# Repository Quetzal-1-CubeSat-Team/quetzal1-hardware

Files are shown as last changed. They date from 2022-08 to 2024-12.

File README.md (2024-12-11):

# Quetzal-1 Hardware

<p align="center">
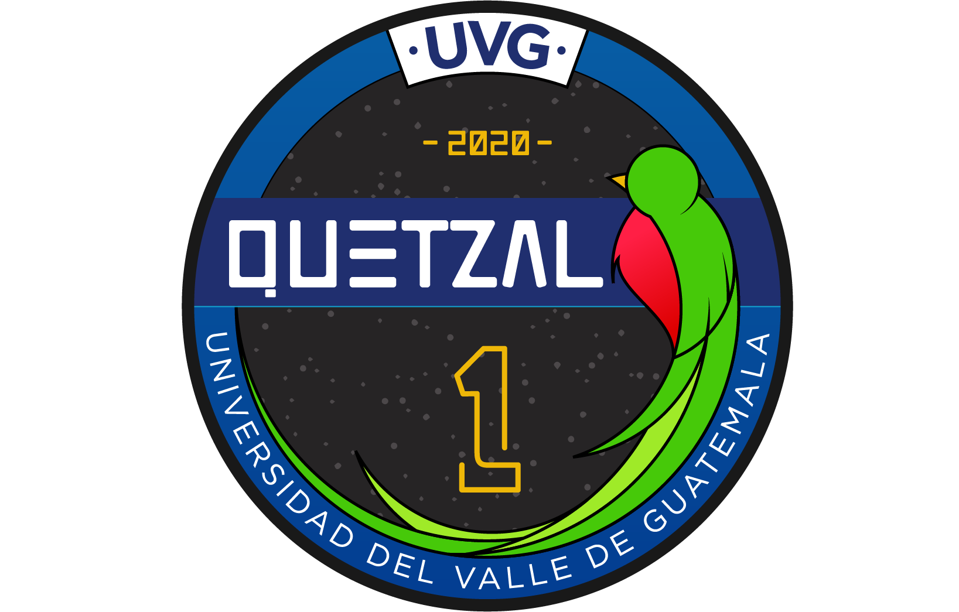
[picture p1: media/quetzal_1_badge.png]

</p>

### 📫 Contact Us!

If the information published here was helpful, we'd love to know! Contact us below and let us know how we can help 🙋‍♀️🙋‍♂️!

1. 💌 **Email us:** [satelite@uvg.edu.gt](mailto:satelite@uvg.edu.gt)
2. 🐦 **Reach out on X:** [@quetzal1_uvg](https://x.com/quetzal1_uvg)

For an overview of Quetzal-1, [read our profile!](https://github.com/Quetzal-1-CubeSat-Team)

## Directory Description

This repository serves as the central location for all hardware design files for the Quetzal-1 satellite. We are indebted to the open-source community, as a large part of the hardware and software was inspired and based on open-source platforms, such as [Arduino](https://www.arduino.cc/), and libraries written by its ever-expanding community.

The hardware files for the following subsystems are included in this repository:

1. [ADCS](./ADCS/): contains the hardware design files for the Attitude Determination and Control System (ADCS).
2. [EPS](./EPS/): contains the hardware design files for the Electrical Power System (EPS).
3. [ADM](./ADM/): contains the hardware design files for the Antenna Deployment Mechanism (ADM).
4. [media](./media/): contains miscellaneous photos relating to the satellite in general, that may be of use and serve as reference to the user.

### Internal Part Naming Scheme

Each Printed Circuit Board (PCB) in the design was tracked according to an internal part number (P/N), which is referenced throughout this repository and especially in the hardware source files. It is as follows:

| System  | P/N | Description |
|---|---|---|
| ADCS | `PT-MIS-PCB-001` | The ADCS PCB, in charge of passive attitude control and attitude determination. |
| EPS | `PT-PWR-EPS-002` | The main EPS PCB, in charge of energy harvesting, storage and distribution. :information_source: Sometimes also referenced as `PT-MIS-PCB-002`. |
| EPS | `PT-MIS-PCB-003`, `-005` through `-008` | The solar panel PCBs for all axes except `Z-`. |
| EPS/ADM | `PT-MIS-PCB-004` | PCB containing both the `Z-` solar panel and the ADM. |

## How should you cite this repository?

You may cite this repository as shown below. Further information is available in the [CITATION.cff](./CITATION.cff) file.

> Quetzal-1 CubeSat Team. (2022). Quetzal-1 Hardware. https://github.com/Quetzal-1-CubeSat-Team/quetzal1-hardware

## Available Repositories

| Repository | Description |
|---|---|
| quetzal1-hardware | This repository. |
| [quetzal1-flight-software](https://github.com/Quetzal-1-CubeSat-Team/quetzal1-flight-software) | Contains the software for Quetzal-1 and its subsystems. |
| [quetzal1-telemetry](https://github.com/Quetzal-1-CubeSat-Team/quetzal1-telemetry) | Contains the telemetry and photos transmitted by Quetzal-1 while in orbit. |
| [gr-quetzal1](https://github.com/danalvarez/gr-quetzal1) | Contains the software used on the Ground Control Station for Quetzal-1, based on GNURadio. |

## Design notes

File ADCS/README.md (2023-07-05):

# Attitude Determination and Control System #

## Directory Description

This directory contains the original design files for the Attitude Determination and Control System (ADCS) Printed Circuit Board (PCB). As with the rest of the Hardware for Quetzal-1, it was developed using [Altium Designer](https://www.altium.com/). It also contains schematics and PCB prints in PDF format so users can understand the overall design without necessary access to Altium's proprietary software.

The directory is organized as follows:

1. `src/`: contains the original design files.
2. `output/`: contains project schematics and PCB prints in PDF format, as well as fabrication files (Gerber and NC Drill). It also contains the reference Bill of Materials (BOM) for the PCB.
3. `media/`: contains miscellaneous photos of the PCB that may be of use and serve as reference to the user.

## Conceptual Design Overview

### Passive Magnetic Attitude Control

The ADCS was developed in-house, and it included a passive control system based on a previous mission by a different team: [Colorado Student Space Weather Experiment (CSSWE)](https://lasp.colorado.edu/home/csswe/). Quetzal-1’s ADCS used a cylindrical magnet ([K&J Magnetics, Cat. No. D84](https://www.kjmagnetics.com/proddetail.asp?prod=D84)) (with a measured 0.74  $A \cdot m^2$ magnetic moment) to align the satellite to Earth’s magnetic field and two hysteresis rods, located on mutually orthogonal axes, to stabilize its rotation [[1]](#user-content-references).

### Attitude Determination

For attitude determination, Quetzal-1's ADCS included an [Adafruit Breakout Board](https://learn.adafruit.com/adafruit-bno055-absolute-orientation-sensor) for an Inertial Measurement Unit (IMU) ([Bosch, Cat. No. BNO055](https://cdn-learn.adafruit.com/assets/assets/000/036/832/original/BST_BNO055_DS000_14.pdf)), which includes a 3-axis accelerometer, gyroscope and magnetometer, as well as a temperature sensor. The accelerometer, however, was flown powered off as linear acceleration data while in free fall was deemed of little value on orbit [[1]](#user-content-references).

Additionally, 12 photodiodes ([Vishay, Cat. No. TEMD6010FX01](https://www.vishay.com/en/product/81308/)) were implemented as Sun sensors, two on each face of the satellite (for redundancy). The selected photodiodes were digitized via a voltage divider and an Analog-to-Digital Converter (ADC) ([Texas Instruments, Cat. No. ADC128D818](https://www.ti.com/product/ADC128D818)). All sensors were sampled and controlled by a microcontroller ([Microchip, Cat. No. ATMEGA328P](https://www.microchip.com/en-us/product/ATmega328P)) on the ADCS PCB [[1]](#user-content-references).

The following diagram gives on overview of the electrical interconnections between the aforementioned components.

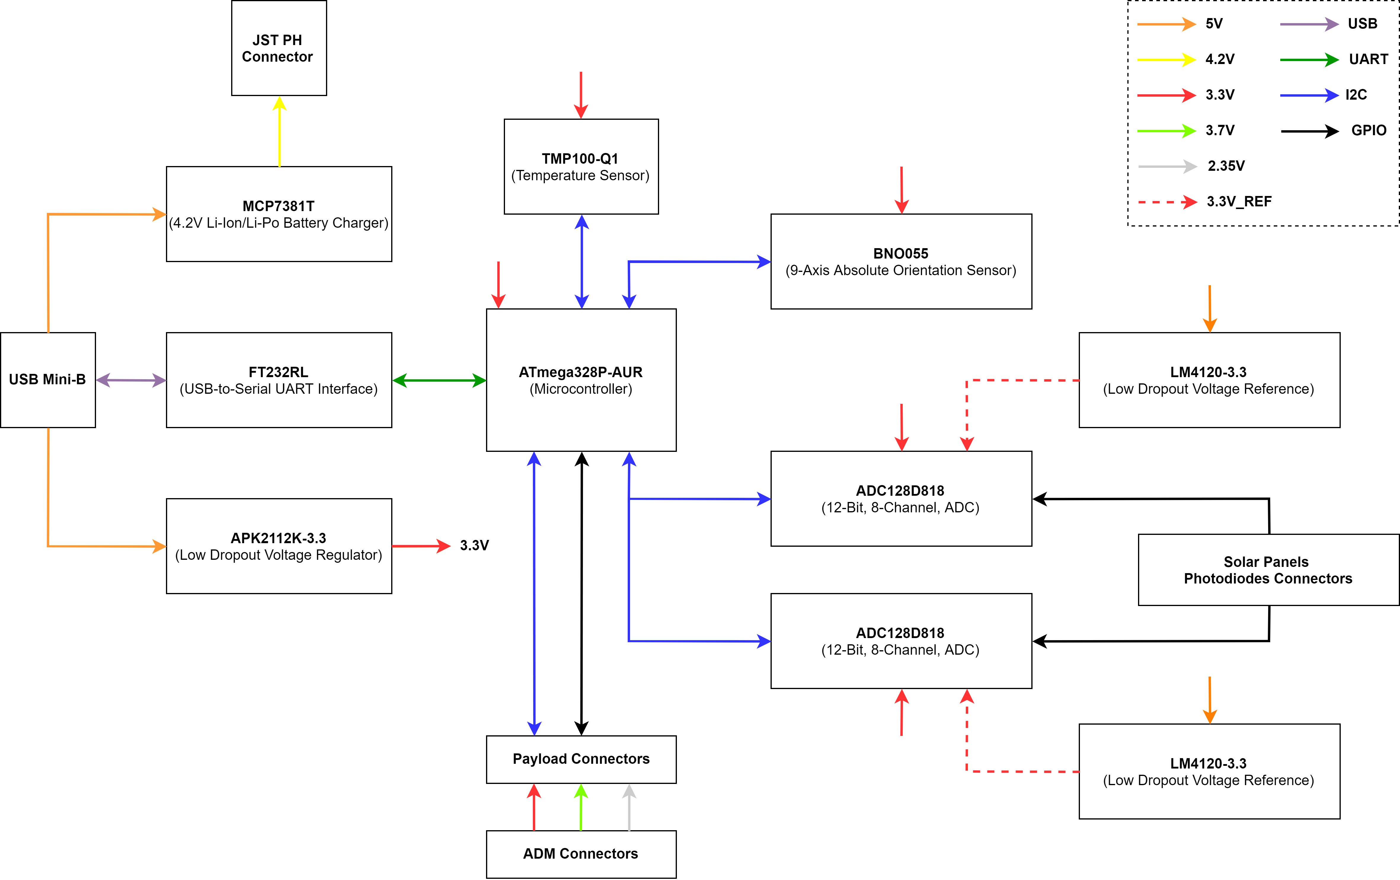
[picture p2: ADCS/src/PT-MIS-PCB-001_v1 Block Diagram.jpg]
adcs-block-diagram ADCS Block Diagram


---
**NOTES**

:warning: The photodiodes were the only ADCS components not mounted on this PCB. They were mounted on each solar panel (`PT-MIS-PCB-003` through `-008`).

:information_source: The attitude determination algorithm was based on the SVD method proposed by [[2]](#user-content-references) and was performed on the ground ex post facto.

:information_source: Further information regarding a component selection rationale, in-orbit performance results and an in-depth analysis of this system's behaviour is provided in [[1]](#user-content-references).

---

## Electrical Design Specifics

### I2C Isolation

The ADCS module communicates via I2C with the On-Board Computer (OBC). However, the Electrical Power System (EPS) PCB contains load switches that turn the ADCS PCB (and other systems) on and off independently. Therefore, the I2C bus on the ADCS PCB was isolated with an I2C buffer ([Texas Instruments, Cat. No. TCA4311ADGKR](https://www.ti.com/product/TCA4311A/part-details/TCA4311ADGKR)). Without this, a power-off of the ADCS PCB would cause the unpowered slave to pull the whole satellite's I2C bus low.

### Deployment Switches

Although the satellite's deployment switches (used to control satellite power-on when deployed from the JEM Small Satellite Deployer [J-SSOD]) were controlled by the EPS PCB, these were physically mounted on the ADCS PCB. This is the reason for the cutouts on opposing corners of the PCB. The switches can be clearly seen in the upper-left and lower-right corners of the PCB in `media/adcs-engineering-model-test-1.jpg`.

### Additional Hardware for Testing and Software Development

The ADCS PCB contained additional hardware that was only used during the development of the module's software and for other testing purposes. Those components that were not to be mounted for the flight model of the PCB, were clearly designated in the design notes of the schematic.

These testing components include:

1. A battery charging circuit ([Microchip Cat. No. MCP73811](https://www.microchip.com/en-us/product/MCP73811)), since the PCB could be powered on by an external battery when not integrated to the rest of the satellite. A P-Channel MOSFET ([Diodes, Cat. No. DMG3415U](https://www.digikey.com/en/products/detail/diodes-incorporated/DMG3415U-7/2052768)) was used to select between the `5V` and `VBAT` power sources.
2. A 3.3 V voltage regulator ([Diodes, Cat. No. AP2112K](https://www.diodes.com/assets/Datasheets/AP2112.pdf)), which could be used to power all components on the board when not connected to the EPS power rails.
3. A USB to UART Serial Interface ([FTDI, Cat. No. FT232RL](https://ftdichip.com/products/ft232rl/)), used to easily program the microcontroller for software development purposes. Note that the [Arduino bootloader](https://docs.arduino.cc/hacking/software/Bootloader) was burned to the microcontroller to permit UART programming. For flight, the microcontroller was programmed via the included ICSP header and an external programmer.

    ---
    :information_source: For future revisions of this board, it may be more convenient to use an external USB to UART converter.

    ---

4. Miscellaneous LEDs and resistors (for I2C address selection and I2C bus pull-up, for example) that were not to be mounted for flight.

## References

[1] Alvarez, D. et al. (2023): Design and On-Orbit Performance of the Attitude Determination and Passive Control System for the Quetzal-1 CubeSat, Journal of Small Satellites (JOSS), vol. 12(2), p. 1231–1247.

[2] Markley, F.L. (1988): Attitude Determination Using Vector Observations and the Singular Value Decomposition, Journal of the Astronautical Sciences, vol. 36(3), pp. 245–258, http://www.malcolmdshuster.com/FC_Markley_1988_J_SVD_JAS_MDSscan.pdf, (accessed October 18, 2021).

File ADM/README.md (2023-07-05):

# Antenna Deployment Mechanism #

## Directory Description

This directory contains the original design files for the Antenna Deployment Mechanism (ADM) Printed Circuit Board (PCB). As with the rest of the Hardware for Quetzal-1, it was developed using [Altium Designer](https://www.altium.com/). It also contains schematics and PCB prints in PDF format so users can understand the overall design without necessary access to Altium's proprietary software.

The directory is organized as follows:

1. `src/`: contains the original design files.
2. `output/`: contains project schematics and PCB prints in PDF format, as well as fabrication files (Gerber and NC Drill). It also contains the reference Bill of Materials (BOM) for the PCB.
3. `media/`: contains miscellaneous photos of the PCB that may be of use and serve as reference to the user.

## Conceptual Design Overview

The following diagram gives an overview of the components mounted on this PCB (and their interconnections). Please note that this PCB houses both the Antenna Deployment Mechanism, as well as the solar panel corresponding to the satellite's `Z-` axis.

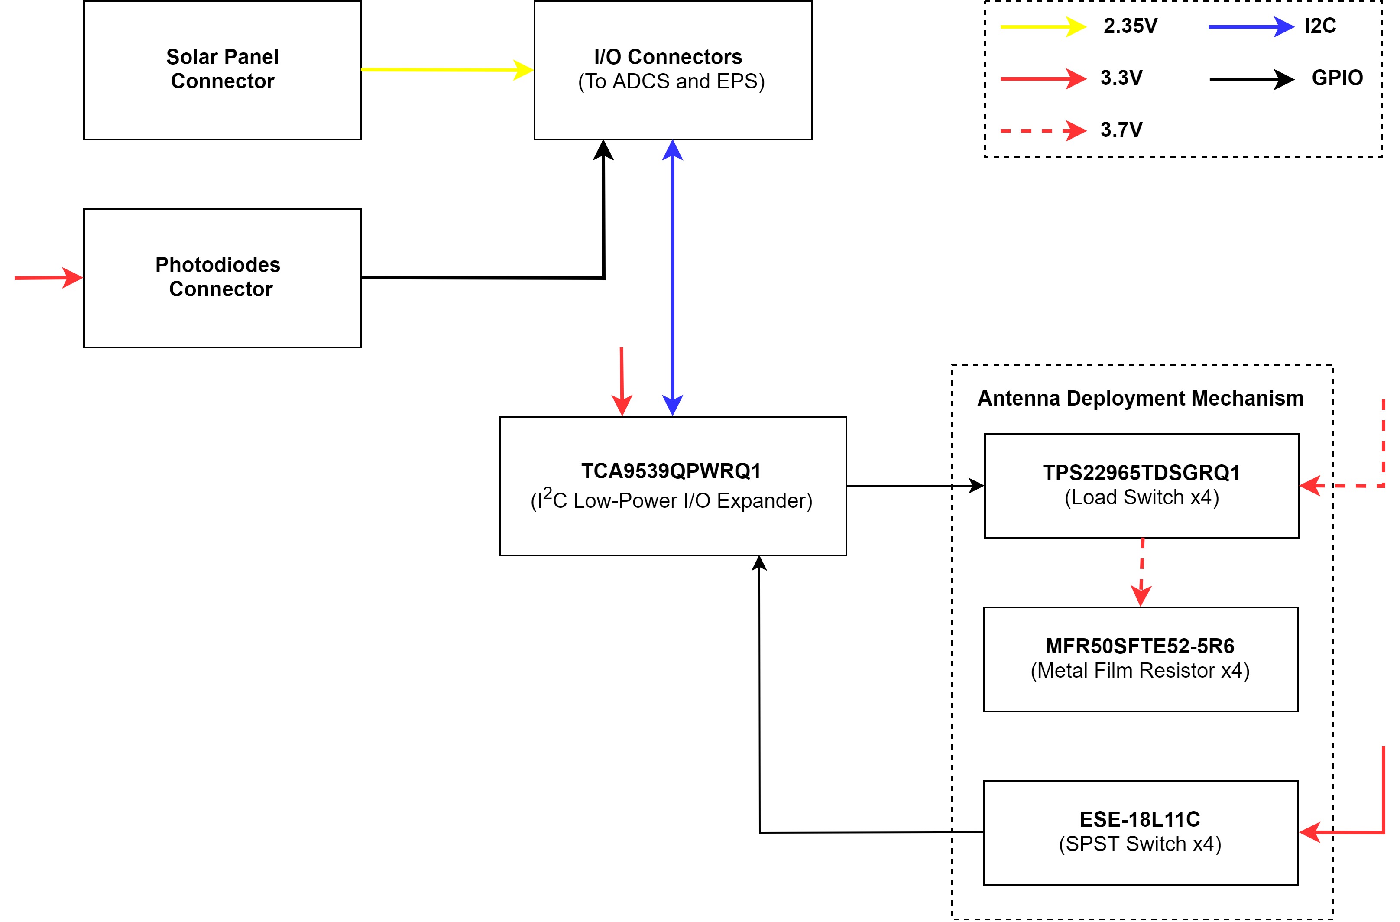
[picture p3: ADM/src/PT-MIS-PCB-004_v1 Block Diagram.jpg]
adm-block-diagram ADM Block Diagram


### Antenna Deployment Mechanism

The mode of operation for this subsystem is, conceptually, quite simple: it is in charge of releasing the satellite's 4 antennas ([GOMspace, Cat. No. NanoCom ANT430](https://gomspace.com/shop/subsystems/communication-systems/nanocom-ant430.aspx)), 30 minutes after deployment from the International Space Station.

While in storage, each antenna is tied to this PCB using general-purpose, 0.3 mm, nylon fishing line (see `media/` for pictures). The line is knot in such a way that it is also tied around a 5.6 Ohm resistor ([Yageo, Cat. No. MFR50SFTE52-5R6](https://www.digikey.com/es/products/detail/yageo/MFR50SFTE52-5R6/9151636)) that is directly connected to the battery via a load switch ([Texas Instruments, Cat. No. TPS22965](https://www.ti.com/product/TPS22965)). The load switches are controlled via I2C by the Electrical Power System (EPS). When the On-Board Computer determines the 30-minute timer after deployment has expired, it commands the EPS to activate each load switch sequentially, dissipating approximately 3.15 W in the resistors (which are rated for 0.5 W) when the battery is fully-charged. This heats the resistors, thereby melting the fishing line which is wrapped around it. When it melts, the antenna (which is spring loaded) releases and an SPST switch ([Panasonic, Cat. No. ESE18L11C](https://na.industrial.panasonic.com/products/electromechanical/switches/lineup/detector-switches/series/28913/model/28919)), which is normally closed when the antenna is stowed, is used to detect the separation. Each of the switches is connected to the EPS via an I2C GPIO Expander ([Texas Instruments, Cat. No. TCA9539QPWRQ1](https://www.ti.com/product/TCA9539-Q1/part-details/TCA9539QPWRQ1)), to inform the system when each antenna has successfully deployed.

The fishing line knot was tested thoroughly on-ground to ensure the highest possible reliability. It was very important that when the fishing line melted, the antennas released completely and would not become stuck with the fishing line. The following diagram describes the knot that was used:

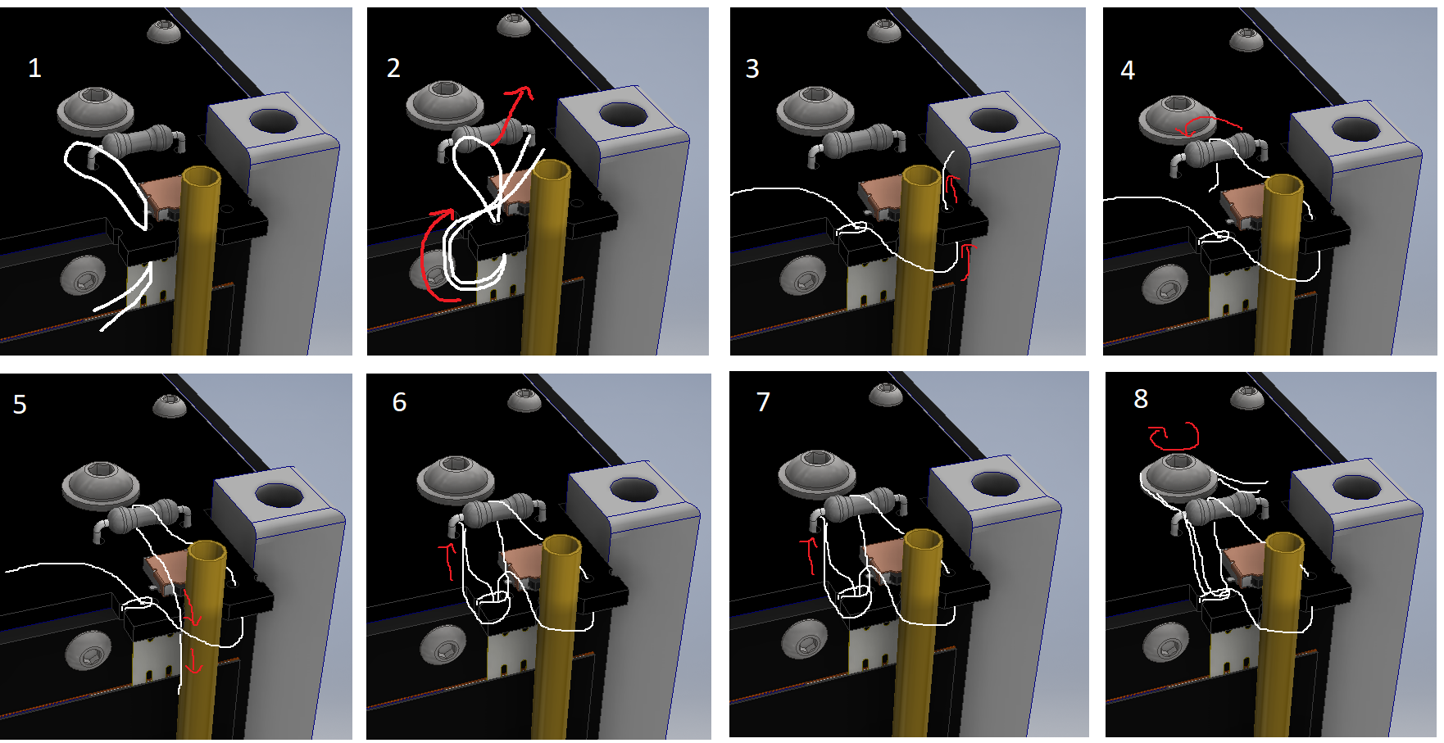
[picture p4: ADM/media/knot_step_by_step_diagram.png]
knot-step-by-step-diagram Antenna Knot Diagram


Additional pictures of the knot can be found in `media/`.

### Solar Panel

This PCB also houses one (1) [AZUR SPACE 3G30A](http://www.azurspace.com/images/products/0003401-01-01_DB_3G30A.pdf) solar cell and two (2) [Vishay TEMD6010FX01](https://www.vishay.com/en/product/81308/) photodiodes (for energy harvesting and attitude determination, respectively).

It only contains one solar cell, as opposed to two, because the satellite's camera points outwards from behind this PCB, and so half of it is reserved for a hole for the camera to see through (see `media/adm_bottom_view_1.jpg` in this directory).

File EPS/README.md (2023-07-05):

# Electrical Power System #

## Directory Description

This directory contains the original design files for the Electrical Power System (EPS) Printed Circuit Board (PCB). As with the rest of the Hardware for Quetzal-1, it was developed using [Altium Designer](https://www.altium.com/). It also contains schematics and PCB prints in PDF format so users can understand the overall design without necessary access to Altium's proprietary software.

The directory is organized as follows:

1. `src/`: contains the original design files.
2. `output/`: contains project schematics and PCB prints in PDF format, as well as fabrication files (Gerber and NC Drill). It also contains the reference Bill of Materials (BOM).
3. `media/`: contains miscellaneous photos of the PCB that may be of use and serve as reference to the user.

---
:information_source: **NOTE**

The `src/` and `output/` directories are further split into two subdirectories each: `eps/` and `solar_panels/`. The former contains the files relating to the main EPS PCB (`PT-PWR-EPS-002`), while the latter contains the files for the satellite's solar panels. These panels were connected to `PT-PWR-EPS-002` to form the complete Electrical Power System.

---

### Solar Panel Directories

The `solar_panel/` directories contain folders under the following naming scheme: `PT-MIS-PCB-NNN`, where `NNN` corresponds to an internal part number (P/N).

| Internal P/N | Satellite Axis |
|---|---|
| PT-MIS-PCB-003 | Z+ |
| PT-MIS-PCB-005 | X+ |
| PT-MIS-PCB-006 | Y- |
| PT-MIS-PCB-007 | Y+ |
| PT-MIS-PCB-008 | X- |

---
:warning: **NOTE**

The PCB corresponding to the `Z-` axis (`PT-MIS-PCB-004`) is purposely not listed here (nor is it contained in this directory). This is because, this PCB also houses the satellite's Antenna Deployment Mechanism (ADM). See the `ADM/` directory for the files pertaining to this subsystem (and further information on the solar cell mounted on this PCB).

---

All solar panels contained in this directory have two (2) [AZUR SPACE 3G30A](http://www.azurspace.com/images/products/0003401-01-01_DB_3G30A.pdf) solar cells and two (2) [Vishay TEMD6010FX01](https://www.vishay.com/en/product/81308/) photodiodes, with the following notable additions:

1. `PT-MIS-PCB-005` contains, additionally, the Remove Before Flight (RBF) switch: [Cinch 133-3701-401](https://www.belfuse.com/resources/productinformations/cinchconnectivitysolutions/johnson/pi-ccs-john-133-3701-401.pdf).
2. `PT-MIS-PCB-006` contains, additionally, the Flight Preparation Panel (FPP) connector, which is used to interface with the satellite when fully assembled.
3. `PT-MIS-PCB-008` contains, on the internal silk screen, the names of all the students, professors, engineers and volunteers that, at the time of fabrication of this PCB, had participated in this project, contributing to its eventual (and resounding) success. We owe a debt of gratitude to them all.

## Conceptual Design Overview

Quetzal-1 carried an Electrical Power System tasked with:

* __Energy Harvesting:__ Generating power using photovoltaic panels to capture energy from the Sun
* __Energy Storage:__ Storing the power generated by the panels in a rechargeable battery that guaranteed the continuous operation of the satellite during eclipse periods on orbit
* __Energy Distribution:__ Conditioning the generated/stored power and distributing it to the rest of the satellite systems (Command & Data Handling system (CDHS), Communications system (COMMS), Attitude Determination & Control system (ADCS), Payload system, and Antenna Deployment Mechanism (ADM))

The following figure shows a high-level diagram of the system [[1]](#user-content-references).

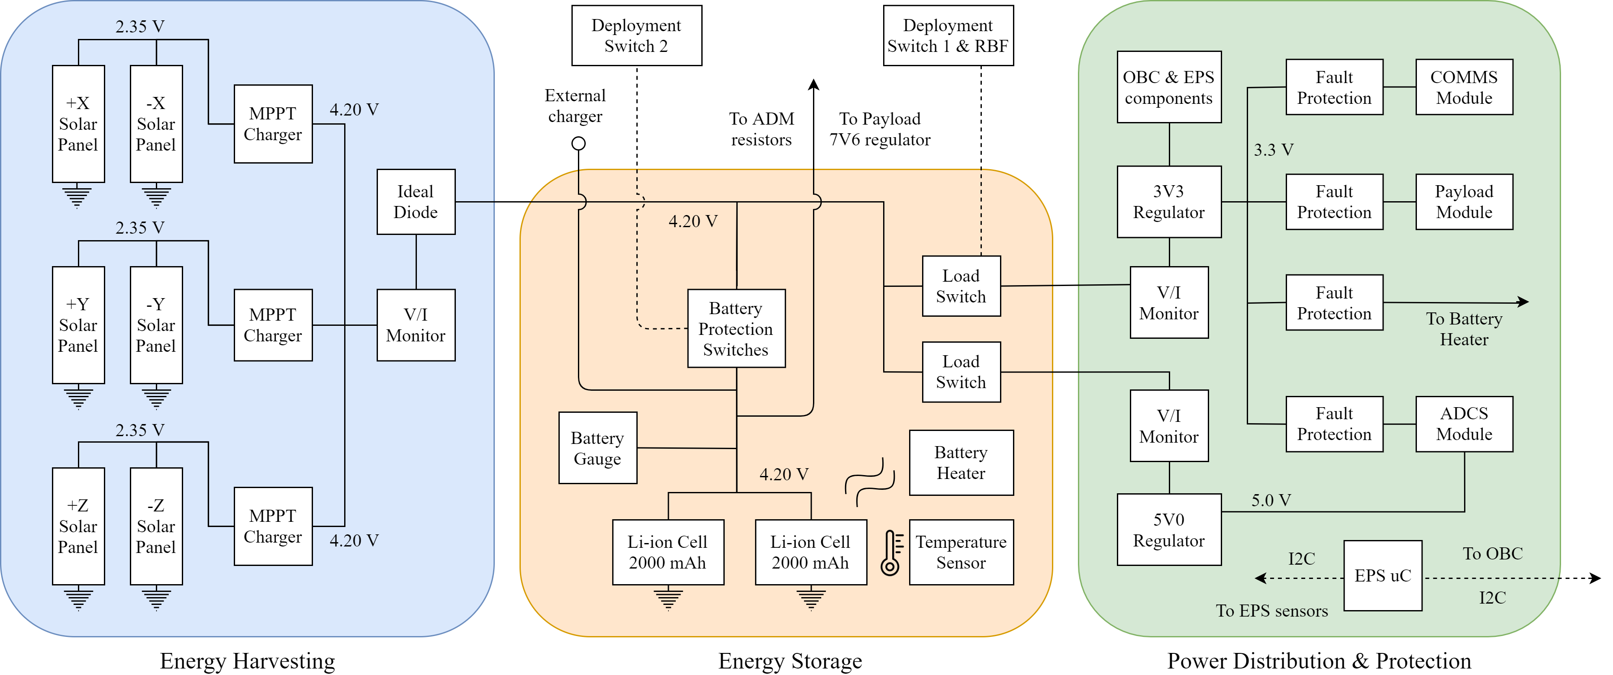
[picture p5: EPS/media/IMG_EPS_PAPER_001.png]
Quetzal-1-Electrical-Power-System-Architecture EPS Architecture


The EPS was also responsible for monitoring the satellite's power grid and relaying the overall health status of the satellite to the on-board computer (OBC). Thus, a microcontroller ([Microchip, Cat. No. ATMEGA328P](https://www.microchip.com/en-us/product/ATmega328P)) was implemented on the EPS circuit board to monitor and manage the power grid following the commands issued by the OBC. This specific microcontroller was chosen because it could operate at 3.3 V (the same voltage as the OBC), and more importantly because its operational temperature range was -40°C to 85°C (ideal to withstand thermal conditions on orbit).

---
:information_source: Further information regarding a component selection rationale, in-orbit performance results and an in-depth analysis of this system's behaviour is provided in [[1]](#user-content-references).

---

## References

[1] Aguilar-Nadalini, A. et al. (2023): Design and On-Orbit Performance of the Electrical Power System for the Quetzal-1 CubeSat, Journal of Small Satellites (JOSS), vol. 12(2), p. 1201–1229.

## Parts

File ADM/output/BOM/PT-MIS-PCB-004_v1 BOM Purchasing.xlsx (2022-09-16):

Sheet: Part List Report
Component List |  |  |  | BOM Purchasing for PT-MIS-PCB-004_v1
 | Source Data From: | PT-MIS-PCB-004_v1.PrjPcb
 | Project: | PT-MIS-PCB-004_v1.PrjPcb
 | Variant: | None
 | Report Date: | 29/11/2018 | 5:53:20 p. m.
 | Print Date: | 2019-03-21 | 12:21:12
# | Category | Manufacturer 1 | Manufacturer Part Number 1 | Package / Case | Description | Quantity | Supplier 1 | Supplier Part Number 1 | Supplier Order Qty 1 | Supplier Unit Price 1 | Supplier Subtotal 1 | Supplier Currency 1
1 | Capacitors | KEMET (https://octopart-clicks.com/click/altium?sku=399-9158-1-ND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) | C0805C104Z3VACTU (https://octopart-clicks.com/click/altium?sku=399-9158-1-ND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) | 0805 (2012 Metric) | CAP CER 0.1UF 25V Y5V 0805 | 1 | Digi-Key | 399-9158-1-ND (https://octopart-clicks.com/click/altium?sku=399-9158-1-ND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) | 10 | 0.08 | 0.81 | USD
2 | Capacitors | Taiyo Yuden (https://octopart-clicks.com/click/altium?sku=587-1300-1-ND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) | LMK212BJ106KG-T (https://octopart-clicks.com/click/altium?sku=587-1300-1-ND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) | 0805 (2012 Metric) | CAP CER 10UF 10V X5R 0805 | 9 | Digi-Key | 587-1300-1-ND (https://octopart-clicks.com/click/altium?sku=587-1300-1-ND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) | 90 | 0.11 | 9.90 | USD
3 | Capacitors | Murata (https://octopart-clicks.com/click/altium?sku=490-10749-1-ND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) | GRM21BR61E226ME44L (https://octopart-clicks.com/click/altium?sku=490-10749-1-ND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) | 0805 (2012 Metric) | CAP CER 22UF 25V X5R 0805 | 4 | Digi-Key | 490-10749-1-ND (https://octopart-clicks.com/click/altium?sku=490-10749-1-ND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) | 40 | 0.44 | 17.40 | USD
4 | Photodiodes | Vishay Semiconductors (https://octopart-clicks.com/click/altium?sku=751-1051-1-ND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) | TEMD6010FX01 (https://octopart-clicks.com/click/altium?sku=751-1051-1-ND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) | - | AMBIENT LIGHTSENSOR MINIFLAT SMD | 2 | Digi-Key | 751-1051-1-ND (https://octopart-clicks.com/click/altium?sku=751-1051-1-ND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) | 20 | 2.00 | 39.96 | USD
5 | Connectors | Wurth Electronics (https://octopart-clicks.com/click/altium?sku=732-5315-ND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) | 61300211121 (https://octopart-clicks.com/click/altium?sku=732-5315-ND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) | - | CONN HEADER 2 POS 2.54 | 3 | Digi-Key | 732-5315-ND (https://octopart-clicks.com/click/altium?sku=732-5315-ND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) | 30 | 0.09 | 2.64 | USD
6 | Connectors | Molex (https://octopart-clicks.com/click/altium?sku=WM7607CT-ND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) | 0533980371 (https://octopart-clicks.com/click/altium?sku=WM7607CT-ND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) | - | CONN HEADER 3POS 1.25MM VERT SMD | 2 | Digi-Key | WM7607CT-ND (https://octopart-clicks.com/click/altium?sku=WM7607CT-ND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) | 10 | 0.99 | 9.90 | USD
7 | Solar Cells | AZUR SPACE | HNR 0003805-01-01 | - | TRIPLE JUNCTION SOLAR CELL ASSEMBLY 3G30A | 1 | AZUR SPACE | HNR 0003805-01-01 | 10 | 500.00 | 5000.00 | USD
8 | Resistors | Yageo (https://octopart-clicks.com/click/altium?sku=311-0.0ARDKR-ND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) | RC0805JR-070RL (https://octopart-clicks.com/click/altium?sku=311-0.0ARDKR-ND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) | 0805 (2012 Metric) | RES SMD 0 OHM JUMPER 1/8W 0805 | 4 | Digi-Key | 311-0.0ARDKR-ND (https://octopart-clicks.com/click/altium?sku=311-0.0ARDKR-ND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) | 40 | 0.03 | 1.09 | USD
9 | Resistors | Yageo (https://octopart-clicks.com/click/altium?sku=311-10.0KCRCT-ND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) | RC0805FR-0710KL (https://octopart-clicks.com/click/altium?sku=311-10.0KCRCT-ND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) | 0805 (2012 Metric) | RES SMD 10K OHM 1% 1/8W 0805 | 15 | Digi-Key | 311-10.0KCRCT-ND (https://octopart-clicks.com/click/altium?sku=311-10.0KCRCT-ND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) | 150 | 0.02 | 2.79 | USD
10 | Resistors | Yageo (https://octopart-clicks.com/click/altium?sku=603-MFR50SFTE52-5R6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) | MFR50SFTE52-5R6 (https://octopart-clicks.com/click/altium?sku=603-MFR50SFTE52-5R6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) | Axial | RES MF 1/2W 1% AXIAL | 4 | Mouser | 603-MFR50SFTE52-5R6 (https://octopart-clicks.com/click/altium?sku=603-MFR50SFTE52-5R6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) | 40 | 0.14 | 5.44 | USD
11 | Switch | Panasonic (https://octopart-clicks.com/click/altium?sku=P14172SCT-ND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) | ESE-18L11C (https://octopart-clicks.com/click/altium?sku=P14172SCT-ND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) | - | SWITCH DETECTOR SPST-NO 10MA 5V | 4 | Digi-Key | P14172SCT-ND (https://octopart-clicks.com/click/altium?sku=P14172SCT-ND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) | 40 | 0.55 | 22.18 | USD
12 | Integrated Circuits | Texas Instruments (https://octopart-clicks.com/click/altium?sku=296-44183-6-ND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) | TCA9539QPWRQ1 (https://octopart-clicks.com/click/altium?sku=296-44183-6-ND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) | 24-TSSOP | IC I/O EXPANDER I2C 16BIT 24TSSOP | 1 | Digi-Key | 296-44183-6-ND (https://octopart-clicks.com/click/altium?sku=296-44183-6-ND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) | 10 | 1.45 | 14.52 | USD
13 | Integrated Circuits | Texas Instruments (https://octopart-clicks.com/click/altium?sku=296-38290-1-ND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) | TPS22965TDSGRQ1 (https://octopart-clicks.com/click/altium?sku=296-38290-1-ND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) | 8-WFDFN Exposed Pad | IC LOAD SWITCH 6A 8WSON | 4 | Digi-Key | 296-38290-1-ND (https://octopart-clicks.com/click/altium?sku=296-38290-1-ND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) | 40 | 0.89 | 35.72 | USD
 |  |  |  |  |  | 54 |  |  | 530 |  | 5162.35
Approved: |  |  |  | Notes:
 |  |  |  |  |  | 10 | pcs: | Total |  | 5162.35 | USD
 |  |  |  |  |  |  |  | Price for 1pcs |  | 516.24 | USD

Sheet: Project Information
Project Full Path | C:\Users\josea\Desktop\2018\UVG 2018\Research\CubeSat\Hardware\Altium\Flight Boards\PT-MIS-PCB-004_v1\PT-MIS-PCB-004_v1.PrjPcb
Project Filename | PT-MIS-PCB-004_v1.PrjPcb
Variant Name | None
Data-Source Filename | PT-MIS-PCB-004_v1.PrjPcb
Data-Source Full Path | C:\Users\josea\Desktop\2018\UVG 2018\Research\CubeSat\Hardware\Altium\Flight Boards\PT-MIS-PCB-004_v1\PT-MIS-PCB-004_v1.PrjPcb
Title | PT-MIS-PCB-004 BOM Purchasing For Project [PT-MIS-PCB-004_v1.PrjPcb] (No PCB Document Selected)
Total Quantity | 64
Report Time | 5:53:20 p. m.
Report Date | 29/11/2018
Report Date & Tine | 29/11/2018 5:53:20 p. m.
Output Name | PT-MIS-PCB-004 BOM Purchasing
Output Type | BOM_PartType
Output Generator Name | BOM
Output Generator Description | Bill of Materials

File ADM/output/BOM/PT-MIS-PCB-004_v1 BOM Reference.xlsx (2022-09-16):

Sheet: Part List Report
Component Reference List |  |  |  | BOM Reference for PT-MIS-PCB-004_v1
 | Source Data From: | PT-MIS-PCB-004_v1.PrjPcb
 | Project: | PT-MIS-PCB-004_v1.PrjPcb
 | Variant: | None
 | Report Date: | 3/12/2018 | 6:52:39 p. m.
 | Print Date: | 2019-03-21 | 12:36:09
# | Designator | Comment | Description | Manufacturer 1 | Manufacturer Part Number 1 | Package / Case | Supplier 1 | Supplier Part Number 1 | UVG Part Number
1 | C1 | C0805C104Z3VACTU | CAP CER 0.1UF 25V Y5V 0805 | KEMET (https://octopart-clicks.com/click/altium?sku=399-9158-1-ND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) | C0805C104Z3VACTU (https://octopart-clicks.com/click/altium?sku=399-9158-1-ND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) | 0805 (2012 Metric) | Digi-Key | 399-9158-1-ND (https://octopart-clicks.com/click/altium?sku=399-9158-1-ND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)
2 | C2, C3, C4, C6, C7, C9, C10, C12, C13 | LMK212BJ106KG-T | CAP CER 10UF 10V X5R 0805 | Taiyo Yuden (https://octopart-clicks.com/click/altium?sku=587-1300-1-ND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) | LMK212BJ106KG-T (https://octopart-clicks.com/click/altium?sku=587-1300-1-ND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) | 0805 (2012 Metric) | Digi-Key | 587-1300-1-ND (https://octopart-clicks.com/click/altium?sku=587-1300-1-ND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)
3 | C5, C8, C11, C14 | GRM21BR61E226ME44L | CAP CER 22UF 25V X5R 0805 | Murata (https://octopart-clicks.com/click/altium?sku=490-10749-1-ND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) | GRM21BR61E226ME44L (https://octopart-clicks.com/click/altium?sku=490-10749-1-ND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) | 0805 (2012 Metric) | Digi-Key | 490-10749-1-ND (https://octopart-clicks.com/click/altium?sku=490-10749-1-ND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)
4 | D1, D2 | TEMD6010FX01 | AMBIENT LIGHTSENSOR MINIFLAT SMD | Vishay Semiconductors (https://octopart-clicks.com/click/altium?sku=751-1051-1-ND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) | TEMD6010FX01 (https://octopart-clicks.com/click/altium?sku=751-1051-1-ND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) | - | Digi-Key | 751-1051-1-ND (https://octopart-clicks.com/click/altium?sku=751-1051-1-ND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)
5 | P1, P2, P3 | 61300211121 | CONN HEADER 2 POS 2.54 | Wurth Electronics (https://octopart-clicks.com/click/altium?sku=732-5315-ND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) | 61300211121 (https://octopart-clicks.com/click/altium?sku=732-5315-ND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) | - | Digi-Key | 732-5315-ND (https://octopart-clicks.com/click/altium?sku=732-5315-ND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)
6 | P4, P5 | 0533980371 | CONN HEADER 3POS 1.25MM VERT SMD | Molex (https://octopart-clicks.com/click/altium?sku=WM7607CT-ND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) | 0533980371+ (https://octopart-clicks.com/click/altium?sku=WM7607CT-ND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) | - | Digi-Key | WM7607CT-ND (https://octopart-clicks.com/click/altium?sku=WM7607CT-ND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)
7 | PV1 | HNR 0003805-01-01 | TRIPLE JUNCTION SOLAR CELL ASSEMBLY 3G30A | AZUR SPACE | HNR 0003805-01-01 | - | AZUR SPACE | HNR 0003805-01-01
8 | R1, R2, R5, R6 | RC0805JR-070RL | RES SMD 0 OHM JUMPER 1/8W 0805 | Yageo (https://octopart-clicks.com/click/altium?sku=311-0.0ARDKR-ND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) | RC0805JR-070RL (https://octopart-clicks.com/click/altium?sku=311-0.0ARDKR-ND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) | 0805 (2012 Metric) | Digi-Key | 311-0.0ARDKR-ND (https://octopart-clicks.com/click/altium?sku=311-0.0ARDKR-ND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)
9 | R3, R4, R7, R12, R13, R14, R15, R16, R17, R18, R19, R20, R21, R23, R24 | RC0805FR-0710KL (https://octopart-clicks.com/click/altium?sku=311-10.0KCRCT-ND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) | RES SMD 10K OHM 1% 1/8W 0805 | Yageo (https://octopart-clicks.com/click/altium?sku=311-10.0KCRCT-ND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) | RC0805FR-0710KL (https://octopart-clicks.com/click/altium?sku=311-10.0KCRCT-ND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) | 0805 (2012 Metric) | Digi-Key | 311-10.0KCRCT-ND (https://octopart-clicks.com/click/altium?sku=311-10.0KCRCT-ND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)
10 | R8, R9, R10, R11 | MFR50SFTE52-5R6 (https://octopart-clicks.com/click/altium?sku=603-MFR50SFTE52-5R6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) | RES MF 1/2W 1% AXIAL | Yageo (https://octopart-clicks.com/click/altium?sku=603-MFR50SFTE52-5R6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) | MFR50SFTE52-5R6 (https://octopart-clicks.com/click/altium?sku=603-MFR50SFTE52-5R6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) | Axial | Mouser | 603-MFR50SFTE52-5R6 (https://octopart-clicks.com/click/altium?sku=603-MFR50SFTE52-5R6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)
11 | S1, S2, S3, S4 | ESE-18L11C | SWITCH DETECTOR SPST-NO 10MA 5V | Panasonic (https://octopart-clicks.com/click/altium?sku=P14172SCT-ND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) | ESE-18L11C (https://octopart-clicks.com/click/altium?sku=P14172SCT-ND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) | - | Digi-Key | P14172SCT-ND (https://octopart-clicks.com/click/altium?sku=P14172SCT-ND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)
12 | U1 | TCA9539QPWRQ1 | IC I/O EXPANDER I2C 16BIT 24TSSOP | Texas Instruments (https://octopart-clicks.com/click/altium?sku=296-44183-6-ND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) | TCA9539QPWRQ1 (https://octopart-clicks.com/click/altium?sku=296-44183-6-ND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) | 24-TSSOP | Digi-Key | 296-44183-6-ND (https://octopart-clicks.com/click/altium?sku=296-44183-6-ND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)
13 | U2, U3, U4, U5 | TPS22965TDSGRQ1 | IC LOAD SWITCH 6A 8WSON | Texas Instruments (https://octopart-clicks.com/click/altium?sku=296-38290-1-ND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) | TPS22965TDSGRQ1 (https://octopart-clicks.com/click/altium?sku=296-38290-1-ND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) | 8-WFDFN Exposed Pad | Digi-Key | 296-38290-1-ND (https://octopart-clicks.com/click/altium?sku=296-38290-1-ND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)
Approved: |  |  |  | Notes:

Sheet: Project Information
Project Full Path | C:\Users\josea\Desktop\2018\UVG 2018\Research\CubeSat\Hardware\Altium\Flight Boards\PT-MIS-PCB-004_v1\PT-MIS-PCB-004_v1.PrjPcb
Project Filename | PT-MIS-PCB-004_v1.PrjPcb
Variant Name | None
Data-Source Filename | PT-MIS-PCB-004_v1.PrjPcb
Data-Source Full Path | C:\Users\josea\Desktop\2018\UVG 2018\Research\CubeSat\Hardware\Altium\Flight Boards\PT-MIS-PCB-004_v1\PT-MIS-PCB-004_v1.PrjPcb
Title | PT-MIS-PCB-004_v1.PrjPcb
Total Quantity | 64
Report Time | 6:52:39 p. m.
Report Date | 3/12/2018
Report Date & Tine | 3/12/2018 6:52:39 p. m.
Output Name | PT-MIS-PCB-004 BOM Reference
Output Type | BOM_PartType
Output Generator Name | BOM
Output Generator Description | Bill of Materials

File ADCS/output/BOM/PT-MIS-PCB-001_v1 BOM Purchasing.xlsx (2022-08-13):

 | Component List |  |  | PT-MIS-PCB-001_v1.1 BOM Purchasing
 | Source Data From: | PT-MIS-PCB-001_v1.PrjPCB
 | Project: | PT-MIS-PCB-001_v1.PrjPCB
 | Variant: | None
 | Report Date: | 26/02/2019 | 3:55:29 p. m.
 | Print Date: | 2019-04-24 | 12:24:29
# | Category | Manufacturer 1 | Manufacturer Part Number 1 | Package / Case | Description | Quantity | Supplier 1 | Supplier Part Number 1 | Supplier Order Qty 1 | Supplier Unit Price 1 | Supplier Subtotal 1 | Supplier Currency 1
1 | Capacitors | KEMET | C0805C104Z3VACTU | 0805 (2012 Metric) | CAP CER 0.1UF 25V Y5V 0805 | 4 | Digi-Key | 399-9158-1-ND | 40 | 0.08 | 3.24 | USD
2 | Capacitors | Kyocera AVX | F921C105MPA | 0805 (2012 Metric) | CAP TANT 1UF 16V 20% 0805 | 2 | Digi-Key | 478-8126-6-ND | 20 | 0.26 | 5.22 | USD
3 | Capacitors | Yageo | CC0805KRX7R9BB223 | 0805 (2012 Metric) | CAP CER 0.022UF 50V X7R 0805 | 2 | Digi-Key | 311-1138-1-ND | 20 | 0.09 | 1.76 | USD
4 | Capacitors | Taiyo Yuden | LMK212BJ106KG-T | 0805 (2012 Metric) | CAP CER 10UF 10V X5R 0805 | 4 | Digi-Key | 587-1300-1-ND | 40 | 0.19 | 7.60 | USD
5 | Capacitors | TDK | C2012X7R1H104K085AA | 0805 (2012 Metric) | CAP CER 0.1UF 50V X7R 0805 | 3 | Digi-Key | 445-7534-1-ND | 30 | 0.14 | 4.08 | USD
6 | Capacitors | KEMET | C0805C180J5GACTU | 0805 (2012 Metric) | CAP CER 18PF 50V NP0 0805 | 2 | Digi-Key | 399-1112-1-ND | 20 | 0.11 | 2.26 | USD
7 | Capacitors | Yageo | CC0805KKX7R7BB105 | 0805 (2012 Metric) | CAP CER 1UF 16V X7R 0805 | 2 | Digi-Key | 311-1365-1-ND | 20 | 0.18 | 3.64 | USD
8 | LEDs | Kingbright | APT1608SYCK | 0603 (1608 Metric) | LED YELLOW CLEAR CHIP SMD | 3 | Digi-Key | 754-1124-1-ND | 30 | 0.24 | 7.06 | USD
9 | Discrete Semiconductors | ON Semiconductor | MBR120VLSFT3G | SOD-123F | DIODE SCHOTTKY 20V 1A SOD123FL | 1 | Digi-Key | MBR120VLSFT3GOSCT-ND | 10 | 0.34 | 3.38 | USD
10 | Connectors | Molex | 0532610371 | - | CONN HEADER SMD R/A 3POS 1.25MM | 4 | Digi-Key | WM7621CT-ND | 40 | 1.05 | 41.80 | USD
11 | Connectors | Molex | 53047-0310 | - | CONN HEADER VERT 3POS 1.25MM | 3 | Digi-Key | WM1732-ND | 30 | 0.41 | 12.39 | USD
12 | Connectors | Amphenol FCI | 10033526-N3212LF | - | CONN RCPT MINI USB B 5POS SMD RA | 1 | Digi-Key | 609-4700-1-ND | 10 | 0.70 | 7.02 | USD
13 | Connectors | Amphenol FCI | 67997-106HLF | - | CONN HEADER VERT 6POS 2.54MM | 1 | Digi-Key | 609-3393-ND | 10 | 1.57 | 15.68 | USD
14 | Connectors | JST | S2B-PH-SM4-TB(LF)(SN) | - | CONN HEADER SMD R/A 2POS 2MM | 1 | Digi-Key | 455-1749-1-ND | 10 | 0.55 | 5.47 | USD
15 | Connectors | Molex | 53398-0671 | - | CONN HEADER SMD 6POS 1.25MM | 1 | Digi-Key | WM7610DKR-ND | 10 | 1.26 | 12.60 | USD
16 | Connectors | Wurth Electronics | 61300211121 | - | CONN HEADER VERT 2POS 2.54MM | 3 | Digi-Key | 732-5315-ND | 30 | 0.09 | 2.64 | USD
17 | Connectors | Molex | 53398-0471 | - | CONN HEADER SMD 4POS 1.25MM | 1 | Digi-Key | WM7608CT-ND | 10 | 1.04 | 10.44 | USD
18 | Discrete Semiconductors | Diodes | DMG3415U-7 | SOT-23-3 | MOSFET P-CH 20V 4A SOT-23-3 | 1 | Digi-Key | DMG3415UDICT-ND | 10 | 0.54 | 5.40 | USD
19 | Resistors | Panasonic | ERA6AEB5902V | 0805 (2012 Metric) | RES SMD 59K OHM 0.1% 1/8W 0805 | 12 | Digi-Key | P59KDACT-ND | 120 | 0.12 | 14.18 | USD
20 | Resistors | Susumu | RR1220P-103-D | 0805 (2012 Metric) | RES SMD 10K OHM 0.5% 1/10W 0805 | 16 | Digi-Key | RR12P10.0KDCT-ND | 160 | 0.04 | 6.02 | USD
21 | Resistors | Stackpole Electronics | RNCP0805FTD1K00 | 0805 (2012 Metric) | RES SMD 1K OHM 1% 1/4W 0805 | 5 | Digi-Key | RNCP0805FTD1K00CT-ND | 50 | 0.07 | 3.60 | USD
22 | Resistors | Yageo | RC0805FR-0710KL | 0805 (2012 Metric) | RES SMD 10K OHM 1% 1/8W 0805 | 7 | Digi-Key | 311-10.0KCRCT-ND | 70 | 0.04 | 2.94 | USD
23 | Resistors | Yageo | RC0805FR-0710ML | 0805 (2012 Metric) | RES SMD 10M OHM 1% 1/8W 0805 | 1 | Digi-Key | 311-10.0MCRCT-ND | 10 | 0.04 | 0.42 | USD
24 | Resistors | Stackpole Electronics | RPC0805JT100K | 0805 (2012 Metric) | RES SMD 100K OHM 5% 1/4W 0805 | 2 | Digi-Key | RPC0805JT100KCT-ND | 20 | 0.17 | 3.30 | USD
25 | Switches | ITT C&K | KMR631NGULCLFS | - | SWITCH TACTILE SPST-NO 50MA 32V | 1 | Digi-Key | CKN10685DKR-ND | 10 | 0.35 | 3.50 | USD
26 | Development Boards | Adafruit Industries | 2472 | - | A 9-DOF A O IMU F B - BNO055 | 1 | Digi-Key | 1528-1426-ND | 10 | 34.95 | 349.50 | USD
27 | Integrated Circuits | TI National Semiconductor | ADC128D818CIMTX/NOPB | 16-TSSOP | IC ADC 12BIT 8CH 16TSSOP | 2 | Digi-Key | 296-41182-1-ND | 20 | 4.21 | 84.14 | USD
28 | Integrated Circuits | Texas Instruments | LM4120AIM5-3.3/NOPB | SOT-23-5 | IC VREF SERIES 3.3V SOT23-5 | 2 | Digi-Key | LM4120AIM5-3.3/NOPBDKR-ND | 20 | 1.97 | 39.30 | USD
29 | Integrated Circuits | FTDI | FT232RL-REEL | 28-SSOP | IC USB FS SERIAL UART 28-SSOP | 1 | Digi-Key | 768-1007-6-ND | 10 | 4.05 | 40.50 | USD
30 | Integrated Circuits | Microchip/Atmel | ATMEGA328P-AUR | 32-TQFP | IC MCU 8BIT 32KB FLASH 32TQFP | 1 | Digi-Key | ATMEGA328P-AURCT-ND | 10 | 2.14 | 21.40 | USD
31 | Integrated Circuits | Microchip | MCP73831T-2ATI/OT | SOT-23-5 | IC CONTROLLR LI-ION 4.2V SOT23-5 | 1 | Digi-Key | MCP73831T-2ATI/OTCT-ND | 10 | 0.58 | 5.80 | USD
32 | Integrated Circuits | Diodes | AP2112K-3.3TRG1 | SOT-25 | IC REG LDO 3.3V 0.6A SOT25 | 1 | Digi-Key | AP2112K-3.3TRG1DICT-ND | 10 | 0.36 | 3.62 | USD
33 | Sensors | Texas Instruments | TMP100AQDBVRQ1 | SOT-23-6 | SENSOR DIGITAL -55C-125C SOT23-6 | 1 | Digi-Key | 296-48716-6-ND | 10 | 1.87 | 18.72 | USD
34 | Crystals | Abracon | ABM7-8.000MHZ-D2Y-T | - | CRYSTAL 8.0000MHZ 18PF SMD | 1 | Digi-Key | 535-9831-6-ND | 10 | 0.63 | 6.33 | USD
 |  |  |  |  |  | 94 |  |  | 940 |  | 754.95
Approved: |  |  |  | Notes:
 |  |  |  |  |  | 10 | pcs: | Total |  | 754.95 | USD
 |  |  |  |  |  |  |  | Price for 1pcs |  | 75.49 | USD

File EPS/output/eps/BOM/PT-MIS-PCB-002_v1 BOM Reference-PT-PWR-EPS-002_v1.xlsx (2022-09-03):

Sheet: Part List Report
 | Component Reference List |  |  | <Parameter Project not found>
 |  | Source Data From: | PT-PWR-EPS-002_v1.PrjPcb |  | Contact:
 |  | Project: | PT-PWR-EPS-002_v1.PrjPcb
 |  | Variant: | None
 | Report Date: | 23/07/2019 | 5:23 p. m.
 | Print Date: | 2019-07-23 | 17:24:53
# | Designator | Comment | Description | Manufacturer 1 | Manufacturer Part Number 1 | Package / Case | Supplier 1 | Supplier Part Number 1
1 | C1, C3, C7, C11, C16, C22, C25, C35, C40 | CL10A105KP8NNNC | CAP CER 1UF 10V X5R 0603 | Samsung | CL10A105KP8NNNC |  | Digi-Key | 1276-1182-1-ND
2 | C2, C9, C15, C32, C33 | CL21A226MQQNNNE | CAP CER 22UF 6.3V X5R 0805 | Samsung | CL21A226MQQNNNE |  | Digi-Key | 1276-1100-6-ND
3 | C4, C12, C17 | GRM21BR60G336ME15L | CAP CER 33UF 4V X5R 0805 | Murata | GRM21BR60G336ME15L |  | Digi-Key | 490-16621-1-ND
4 | C5, C6, C13, C14, C18, C19 | CL10C102JB8NNNC | CAP CER 1000PF 50V C0G/NP0 0603 | Sams | CL10C102JB8NNNC |  | Digi-Key | 1276-1091-1-ND
5 | C8 | GRM188R60J226MEA0D | CAP CER 22UF 6.3V X5R 0603 | Murata | GRM188R60J226MEA0D |  | Digi-Key | 490-7611-1-ND
6 | C10, C26, C27, C34, C36, C37, C41, C42, C43, C44, C45, C46, C47, C48, C49, C50, C51, C52, C54, C55, C56, C59 | C0603C104K8RACTU | CAP CER 0.1UF 10V X7R 0603 | KEMET | C0603C104K8RACTU |  | Digi-Key | 399-1095-1-ND
7 | C20 | CL10B474KA8NFNC | CAP CER 0.47UF 25V X7R 0603 | Samsung | CL10B474KA8NFNC |  | Digi-Key | 1276-2082-1-ND
8 | C21, C30, C31, C38, C39 | CL10A106MQ8NNNC | CAP CER 10UF 6.3V X5R 0603 | Samsung | CL10A106MQ8NNNC |  | Digi-Key | 1276-1119-1-ND
9 | C23, C24 | EMK107B7224KA-T | CAP CER 0.22UF 16V X7R 0603
10 | C28, C29, C57 | LMK212BJ106KG-T | CAP CER 10UF 10V X5R 0805 | Taiyo | LMK212BJ106KG-T | 0805 (2012 Metric) | Digi-Key | 587-1300-1-ND
11 | C53 | C2012X7R1H104K085AA | CAP CER 0.1UF 50V X7R 0805 | TDK | C2012X7R1H104K085AA | 0805 (2012 Metric) | Digi-Key | 445-7534-1-ND
12 | C58, C60 | C0805C180J5GAC-TU | CAP CER 18PF 50V C0G/NP0 0805 | KEMET | C0805C180J5GACTU | 805 | Digi-Key | 399-1112-1-ND
13 | C61, C62 | GRM188R60E476ME15D | CAP CER 47UF 2.5V X5R 0603 | Murata | GRM188R60E476ME15D |  | Digi-Key | 490-13245-1-ND
14 | D1, D2, D3, D4, D5, D6 | MBR120VLSFT3G | DIODE SCHOTTKY 20V 1A SOD123FL | ON Semiconductor | MBR120VLSFT3G | SOD-123F | Digi-Key | MBR120VLSFT3GOSCT-ND
15 | D7, D8, D9 | SMM4F5.0A-TR | Diode TVS Single Uni-Dir 5V 400W 2-Pin DO-222AA T/R | STMicroelectronics | SMM4F5.0A-TR |  | Digi-Key | 497-15660-1-ND
16 | D10, D11 | RB051MM-2YTR | DIODE SCHOTTKY 20V 3A PMDU | Rohm | RB051MM-2YTR |  | Digi-Key | RB051MM-2YCT-ND
17 | D12, D14 | APT1608SYCK | LED YELLOW CLEAR CHIP SMD | Kingbright | APT1608SYCK | 0603 (1608 Metric) | Digi-Key | 754-1124-1-ND
18 | D13 | APT1608SGC | LED 1.6X0.8MM 568NM GRN CLR SMD | Kingbright | APT1608SGC | 0603 (1608 Metric) | Digi-Key | 754-1121-1-ND
19 | L1, L2, L3 | SRR1206-100ML | FIXED IND 10UH 3.3A 35 MOHM SMD | Bourns | SRR1206-100ML |  | Digi-Key | SRR1206-100MLCT-ND
20 | L4 | XFL4020-152MEB | FIXED IND 1.5UH 9.1A 15.8 MOHM SMD | Coilcraft | XFL4020-152MEB |  | Mouser | 994-XFL4020-152MEB
21 | P1, P2 | ESQ-126-14-G-D | CONN SOCKET 52POS 0.1 GOLD PCB | Samtec | ESQ-126-14-G-D |  | Digi-Key | SAM11114-ND
22 | P3, P4, P5, P6 | 532610271 | CONN HEADER 2POS 1.25MM R/A SMD | Molex | 53261-0271 |  | Digi-Key | WM7620CT-ND
23 | P7, P8, P10 | 533980271 | CONN HEADER 2POS 1.25MM VERT SMD | Molex | 53398-0271 |  | Digi-Key | WM7606CT-ND
24 | P9 | S2B-PH-SM4-TB(LF)(SN) | CONN HEADER PH SIDE 2POS 2MM SMD | JST | S2B-PH-SM4-TB(LF)(SN) |  | Digi-Key | 455-1749-1-ND
25 | P11 | 533980471 | CONN HEADER 4POS 1.25MM VERT SMD | Molex | 53398-0471 |  | Digi-Key | WM7608CT-ND
26 | P12 | 67997-106HLF | CONN HEADER 6POS .100 STR 30AU | Amphenol FCI | 67997-106HLF |  | Digi-Key | 609-3393-ND
27 | P13 | 10033526-N3212LF | CONN MINI USB RCPT RA TYPE B SMD | Amphenol ICC | 10033526-N3212LF |  | Digi-Key | 609-4700-1-ND
28 | P14, P15 | 61300311121 | CONN HEADER 3 POS 2.54 | Wurth Electronics | 61300311121 |  | Digi-Key | 732-5316-ND
29 | P16 | 61300211121 | CONN HEADER 2 POS 2.54 | Wurth Electronics | 61300211121 |  | Digi-Key | 732-5315-ND
30 | Q1 | CSD16412Q5A | MOSFET N-CH 25V 52A 8SON | Texas Instruments | CSD16412Q5A |  | Digi-Key | 296-24256-1-ND
31 | R1, R2, R16, R17, R25, R26, R27, R30, R37, R38, R48, R49, R54, R75, R80, R82 | RNCP0603FTD10K0 | RES SMD 10K OHM 1% 1/8W 0603 | Stackpole Electronics | RNCP0603FTD10K0 |  | Digi-Key | RNCP0603FTD10K0CT-ND
32 | R3, R11, R19 | RLP73N3AR091FTDF | RES SMD 0.091 OHM 1% 2W 2512 | TE Connectivity | RLP73N3AR091FTDF |  | Digi-Key | A109693CT-ND
33 | R4, R5, R7, R12, R13, R15, R20, R21, R23, R33, R34, R39, R51, R56, R61, R66, R71, R76, R77, R78 | ESR03EZPJ102 | RES SMD 1K OHM 5% 1/4W 0603 | Rohm | ESR03EZPJ102 |  | Digi-Key | RHM1.0KDCT-ND
34 | R6, R14, R22 | RC0603JR-071M2L | RES SMD 1.2M OHM 5% 1/10W 0603 | Yageo | RC0603JR-071M2L |  | Digi-Key | 311-1.2MGRCT-ND
35 | R8, R9, R36, R41, R47, R53 | RMCF0603ZT0R00 | RES SMD 0 OHM JUMPER 1/10W 0603 | Stackpole Electronics | RMCF0603ZT0R00 |  | Digi-Key | RMCF0603ZT0R00CT-ND
36 | R10, R18, R24 | RMCF0603FT510K | RES SMD 510K OHM 1% 1/10W 0603 | Stackpole Electronics | RMCF0603FT510K |  | Digi-Key | RMCF0603FT510KCT-ND
37 | R28 | CSRN2010FK10L0 | RES 0.01 OHM 1% 1W 2010 | Stackpole Electronics | CSRN2010FK10L0 |  | Digi-Key | CSRN2010FK10L0DKR-ND
38 | R29, R35, R42, R50, R59, R64, R69, R74 | CR0603-JW-104ELF | RES SMD 100K OHM 5% 1/10W 0603 | Bourns | CR0603-JW-104ELF |  | Digi-Key | CR0603-JW-104ELFCT-ND
39 | R31 | CRGCQ0603F33K | RES SMD 33K OHM 1% 1/10W 0603 | TE Connectivity | 4-2176339-3 |  | Digi-Key | A129706CT-ND
40 | R32 | RC0603FR-07110KL | RES SMD 110K OHM 1% 1/10W 0603 | Yageo | RC0603FR-07110KL |  | Digi-Key | 311-110KHRCT-ND
41 | R40, R52, R57, R62, R67, R72 | ERJ3EKF7502V | RES SMD 75K OHM 1% 1/10W 0603 | Panasonic | ERJ3EKF7502V |  | Digi-Key | P75.0KHCT-ND
42 | R43, R44 | RC0805FR-0710KL | RES SMD 10K OHM 1% 1/8W 0805 | Yageo | RC0805FR-0710KL |  | Digi-Key | 311-10.0KCRCT-ND
43 | R45 | RNCF0603BTE213K | RES SMD 213K OHM 0.1% 1/10W 0603 | Stackpole Electronics | RNCF0603BTE213K |  | Digi-Key | RNCF0603BTE213KCT-ND
44 | R46 | RMCF0603FT68K1 | RES SMD 68.1K OHM 1% 1/10W 0603 | Stackpole Electronics | RMCF0603FT68K1 |  | Digi-Key | RMCF0603FT68K1CT-ND
45 | R55, R60, R65, R70 | RU1608FR100CS | RES SMD 0.1 OHM 1% 1/4W 0603 | Samsung | RU1608FR100CS |  | Digi-Key | 1276-6155-1-ND
46 | R58, R63, R68, R73 | RC0603JR-0713KL | RES SMD 13K OHM 5% 1/10W 0603 | Yageo | RC0603JR-0713KL |  | Digi-Key | 311-13KGRCT-ND
47 | R79 | RT0805FRE071ML | RES SMD 1M OHM 1% 1/8W 0805 | Yageo | RT0805FRE071ML |  | Digi-Key | YAG3361DKR-ND
48 | R81, R83 | CRGCQ0603F330K | RES SMD 330K OHM 1% 1/10W 0603 | TE Connectivity | CRGCQ0603F330K |  | Digi-Key | A129718CT-ND
49 | S1 | KMR631NGULCLFS | SWITCH TACTILE SPST-NO 50MA 32V | ITT C&K | KMR631NGULCLFS |  | Digi-Key | CKN10685DKR-ND
50 | U1, U9, U12 | INA260AIPWR | IC MONITOR PWR/CURR 16TSSOP | Texas Instruments | INA260AIPWR |  | Digi-Key | 296-47777-1-ND
51 | U2, U4, U5 | SPV1040TTR | IC SOLAR BATTERY CHARGER 8TSSOP | STMicroelectronics | SPV1040TTR |  | Digi-Key | 497-11288-1-ND
52 | U3 | LTC4352IMS#PBF | IC OR CTRLR N+1 12MSOP | Analog Devices / Linear Technology | LTC4352IMS#PBF |  | Digi-Key | LTC4352IMS#PBF-ND
53 | U6 | BQ27441DRZR-G1A | IC BATT FUEL GAUGE LI-ION 12SON | Texas Instruments | BQ27441DRZR-G1A |  | Digi-Key | 296-39941-6-ND
54 | U7, U8 | TPS2557DRBT | IC PWR DIST SWITCH ADJ 8SON | Texas Instruments | TPS2557DRBT |  | Digi-Key | 296-25432-1-ND
55 | U10, U13, U15, U17, U19, U21 | TPS2551QDBVRQ1 | IC POWER-DIST SWITCH ADJ SOT23-6 | Texas Instruments | TPS2551QDBVRQ1 |  | Digi-Key | 296-23692-1-ND
56 | U11 | TPS63070RNMT | IC REG BCK BST ADJ 2A 15VQFN | Texas Instruments | TPS63070RNMT |  | Digi-Key | 296-44764-1-ND
57 | U14 | MCP1252-33X50I/MS | IC REG SWITCHD CAP PROG 8MSOP | Microchip | MCP1252-33X50I/MS |  | Digi-Key | MCP1252-33X50I/MS-ND
58 | U16, U18, U20, U22 | INA169NA/3K | IC CURRENT MONITOR 0.5% SOT23-5 | Texas Instruments | INA169NA/3K |  | Digi-Key | 296-26063-6-ND
59 | U23 | ATMEGA328P-AURCT-ND | IC MCU 8BIT 32KB FLASH 32TQFP | Microchip | ATMEGA328P-AUR | 32-TQFP | Digi-Key | ATMEGA328P-AURCT-ND
60 | U24 | FT232RL-REEL | IC USB FS SERIAL UART 28-SSOP | FTDI | FT232RL-REEL |  | Digi-Key | 768-1007-6-ND
61 | U25 | 74AUP1G08SE-7 | IC GATE AND 1CH 2-INP SOT-353 | Diodes | 74AUP1G08SE-7 |  | Digi-Key | 74AUP1G08SE-7DICT-ND
62 | Y1 | 535-9831-1-ND | CRYSTAL 8.0000MHZ 18PF SMD | Abracon | ABM7-8.000MHZ-D2Y-T |  | Digi-Key | 535-9831-6-ND
Approved: |  |  |  | Notes:

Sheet: Project Information
Project Full Path | C:\Users\josea\Desktop\2018\UVG 2018\Research\CubeSat\Hardware\Altium\Flight Boards\PT-PWR-EPS-002_v1\PT-PWR-EPS-002_v1.PrjPcb
Project Filename | PT-PWR-EPS-002_v1.PrjPcb
Variant Name | None
Data-Source Filename | PT-PWR-EPS-002_v1.PrjPcb
Data-Source Full Path | C:\Users\josea\Desktop\2018\UVG 2018\Research\CubeSat\Hardware\Altium\Flight Boards\PT-PWR-EPS-002_v1\PT-PWR-EPS-002_v1.PrjPcb
Title | PT-PWR-EPS-002_v1.PrjPcb
Total Quantity | 217
Report Time | 5:23 p. m.
Report Date | 23/07/2019
Report Date & Tine | 23/07/2019 5:23 p. m.
Output Name | PT-MIS-PCB-002_v1 BOM Reference
Output Type | BOM_PartType
Output Generator Name | BOM
Output Generator Description | Bill of Materials

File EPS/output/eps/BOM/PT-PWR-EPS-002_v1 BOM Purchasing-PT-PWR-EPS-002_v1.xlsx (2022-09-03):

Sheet: Part List Report
 | Component List |  |  | PT-PWR-EPS-002_v1 BOM Purchasing
 | Source Data From: | PT-PWR-EPS-002_v1.PrjPcb
 | Project: | PT-PWR-EPS-002_v1.PrjPcb
 | Variant: | None
 | Report Date: | 13/06/2019 | 4:23 p. m.
 | Print Date: | 2019-06-13 | 16:56:29
# | Category | Manufacturer 1 | Manufacturer Part Number 1 | Package / Case | Description | Quantity | Supplier 1 | Supplier Part Number 1 | Supplier Order Qty 1 | Supplier Unit Price 1 | Supplier Subtotal 1 | Supplier Currency 1
1 | Capacitors | Samsung | CL10A105KP8NNNC | 0603 (1608 Metric) | CAP CER 1UF 10V X5R 0603 | 9 | Digi-Key | 1276-1182-1-ND | 90 | 0.04 | 3.42 | USD
2 | Capacitors | Samsung | CL21A226MQQNNNE | 0805 (2012 Metric) | CAP CER 22UF 6.3V X5R 0805 | 5 | Digi-Key | 1276-1100-6-ND | 50 | 0.12 | 6.05 | USD
3 | Capacitors | Murata | GRM21BR60G336ME15L | 0805 (2012 Metric) | CAP CER 33UF 4V X5R 0805 | 3 | Digi-Key | 490-16621-1-ND | 30 | 0.70 | 20.97 | USD
4 | Capacitors | Samsung | CL10C102JB8NNNC | 0603 (1608 Metric) | CAP CER 1000PF 50V C0G/NP0 0603 | 6 | Digi-Key | 1276-1091-1-ND | 60 | 0.05 | 2.82 | USD
5 | Capacitors | Murata | GRM188R60J226MEA0D | 0603 (1608 Metric) | CAP CER 22UF 6.3V X5R 0603 | 1 | Digi-Key | 490-7611-1-ND | 10 | 0.18 | 1.77 | USD
6 | Capacitors | KEMET | C0603C104K8RAC7867 | 0603 (1608 Metric) | CAP CER 0.1UF 10V X7R 0603 | 22 | Digi-Key | 399-1095-1-ND | 220 | 0.05 | 11.09 | USD
7 | Capacitors | Samsung | CL10B474KA8NFNC | 0603 (1608 Metric) | CAP CER 0.47UF 25V X7R 0603 | 1 | Digi-Key | 1276-2082-1-ND | 10 | 0.07 | 0.73 | USD
8 | Capacitors | Samsung | CL10A106MQ8NNNC | 0603 (1608 Metric) | CAP CER 10UF 6.3V X5R 0603 | 5 | Digi-Key | 1276-1119-1-ND | 50 | 0.11 | 5.50 | USD
9 | Capacitors | Taiyo Yuden | EMK107B7224KA-T | 0603 (1608 Metric) | CAP CER 0.22UF 16V X7R 0603 | 2 | Digikey | 587-1249-1-ND | 20 | 0.10 | 2.00 | USD
10 | Capacitors | Taiyo Yuden | CELMK212BJ106KG-T | 0805 (2012 Metric) | CAP CER 10UF 10V X5R 0805 | 3 | Digi-Key | 587-1300-1-ND | 30 | 0.11 | 3.39 | USD
11 | Capacitors | TDK | C2012X7R1H104K085AA | 0805 (2012 Metric) | CAP CER 0.1UF 50V X7R 0805 | 1 | Digi-Key | 445-7534-1-ND | 10 | 0.13 | 1.30 | USD
12 | Capacitors | KEMET | C0805C180J5GAC7800 | 0805 (2012 Metric) | CAP CER 18PF 50V C0G/NP0 0805 | 2 | Digi-Key | 399-1112-1-ND | 20 | 0.11 | 2.18 | USD
13 | Capacitors | Murata | GRM188R60E476ME15D | 0603 (1608 Metric) | CAP CER 47UF 2.5V X5R 0603 | 2 | Digi-Key | 490-13245-1-ND | 20 | 0.35 | 7.00 | USD
14 | Discrete Semiconductor | ON Semiconductor | MBR120VLSFT3G | SOD-123F | DIODE SCHOTTKY 20V 1A SOD123FL | 6 | Digi-Key | MBR120VLSFT3GOSCT-ND | 60 | 0.32 | 19.26 | USD
15 | Discrete Semiconductor | STMicroelectronics | SMM4F5.0A-TR | DO222-AA | TVS DIODE 5V 13.4V DO222-AA | 3 | Digi-Key | 497-15660-1-ND | 30 | 0.49 | 14.61 | USD
16 | Discrete Semiconductor | Rohm | RB051MM-2YTR | SOD-123F | DIODE SCHOTTKY 20V 3A PMDU | 2 | Digi-Key | RB051MM-2YCT-ND | 20 | 0.42 | 8.34 | USD
17 | Optoelectronics | Kingbright | APT1608SYCK | 0603 (1608 Metric) | LED YELLOW CLEAR CHIP SMD | 2 | Digi-Key | 754-1124-1-ND | 20 | 0.31 | 6.14 | USD
18 | Optoelectronics | Kingbright | APT1608SGC | 0603 (1608 Metric) | LED 1.6X0.8MM 568NM GRN CLR SMD | 1 | Digi-Key | 754-1121-1-ND | 10 | 0.04 | 0.42 | USD
19 | Inductors | Bourns | SRR1206-100ML | - | FIXED IND 10UH 3.3A 35 MOHM SMD | 3 | Digi-Key | SRR1206-100MLCT-ND | 30 | 1.05 | 31.41 | USD
20 | Inductors | Coilcraft | XFL4020-152MEB | - | FIXED IND 1.5UH 9.1A 15.8 MOHM SMD | 1 | Mouser | 994-XFL4020-152MEB | 10 | 1.99 | 19.90 | USD
21 | Connectors | Samtec | ESQ-126-14-G-D | - | CONN SOCKET 52POS 0.1 GOLD PCB | 2 | Digi-Key | SAM11114-ND | 20 | 8.92 | 178.34 | USD
22 | Connectors | Molex | 532610271 | - | CONN HEADER 2POS 1.25MM R/A SMD | 4 | Digi-Key | WM7620CT-ND | 40 | 0.86 | 34.40 | USD
23 | Connectors | Molex | 533980271 | - | CONN HEADER 2POS 1.25MM VERT SMD | 2 | Digi-Key | WM7606CT-ND | 20 | 0.82 | 16.34 | USD
24 | Connectors | JST | S2B-PH-SM4-TB(LF)(SN) | - | CONN HEADER PH SIDE 2POS 2MM SMD | 1 | Digi-Key | 455-1749-1-ND | 10 | 0.55 | 5.47 | USD
25 | Connectors | Amphenol FCI | 67997-106HLF | - | CONN HEADER 6POS .100 STR 30AU | 1 | Digi-Key | 609-3393-ND | 10 | 1.57 | 15.68 | USD
26 | Connectors | Amphenol ICC | 10033526-N3212LF | - | CONN MINI USB RCPT RA TYPE B SMD | 1 | Digi-Key | 609-4700-1-ND | 10 | 0.70 | 7.02 | USD
27 | Connectors | Molex | 53398-0471 | - | CONN HEADER 4POS 1.25MM VERT SMD | 1 | Digi-Key | WM7608CT-ND | 10 | 1.04 | 10.44 | USD
28 | Connectors | Wurth Electronics | 61300311121 | - | CONN HEADER 3 POS 2.54 | 2 | Digi-Key | 732-5316-ND | 20 | 0.11 | 2.12 | USD
29 | Connectors | Wurth Electronics | 61300211121 | - | CONN HEADER 2 POS 2.54 | 1 | Digi-Key | 732-5315-ND | 10 | 0.11 | 1.06 | USD
30 | Discrete Semiconductor | Texas Instruments | CSD16412Q5A | 8-SON | MOSFET N-CH 25V 52A 8SON | 1 | Digi-Key | 296-24256-1-ND | 10 | 0.87 | 8.72 | USD
31 | Discrete Semiconductor | Texas Instruments | CSD17552Q3A | 8-SON | MOSFET N-CH 30V 15A 8SON | 1 | Digi-Key | 296-34990-1-ND | 10 | 0.90 | 8.97 | USD
32 | Discrete Semiconductor | Texas Instruments | CSD25402Q3A | 8-SON | MOSFET P-CH 20V 76A 8SON | 1 | Digi-Key | 296-38916-1-ND | 10 | 0.82 | 8.21 | USD
33 | Resistors | Stackpole Electronics | RNCP0603FTD10K0 | 0603 (1608 Metric) | RES SMD 10K OHM 1% 1/8W 0603 | 17 | Digi-Key | RNCP0603FTD10K0CT-ND | 170 | 0.03 | 4.64 | USD
34 | Resistors | TE Connectivity | RLP73N3AR091FTDF | 2512 (6332 Metric) | RES SMD 0.091 OHM 1% 2W 2512 | 3 | Digi-Key | A109693CT-ND | 30 | 0.54 | 16.18 | USD
35 | Resistors | Rohm | ESR03EZPJ102 | 0603 (1608 Metric) | RES SMD 1K OHM 5% 1/4W 0603 | 20 | Digi-Key | RHM1.0KDCT-ND | 200 | 0.03 | 6.36 | USD
36 | Resistors | Yageo | RC0603JR-071M2L | 0603 (1608 Metric) | RES SMD 1.2M OHM 5% 1/10W 0603 | 3 | Digi-Key | 311-1.2MGRCT-ND | 30 | 0.02 | 0.60 | USD
37 | Resistors | Stackpole Electronics | RMCF0603ZT0R00 | 0603 (1608 Metric) | RES SMD 0 OHM JUMPER 1/10W 0603 | 6 | Digi-Key | RMCF0603ZT0R00CT-ND | 60 | 0.01 | 0.53 | USD
38 | Resistors | Stackpole Electronics | RMCF0603FT510K | 0603 (1608 Metric) | RES SMD 510K OHM 1% 1/10W 0603 | 3 | Digi-Key | RMCF0603FT510KCT-ND | 30 | 0.02 | 0.51 | USD
39 | Resistors | Stackpole Electronics | CSRN2010FK10L0 | 2010 (5025 Metric) | RES 0.01 OHM 1% 1W 2010 | 1 | Digi-Key | CSRN2010FK10L0DKR-ND | 10 | 0.48 | 4.85 | USD
40 | Resistors | TE Connectivity | 4-2176339-3 | 0603 (1608 Metric) | RES SMD 33K OHM 1% 1/10W 0603 | 1 | Digi-Key | A129706CT-ND | 10 | 0.03 | 0.31 | USD
41 | Resistors | Yageo | RC0603FR-07110KL | 0603 (1608 Metric) | RES SMD 110K OHM 1% 1/10W 0603 | 1 | Digi-Key | 311-110KHRCT-ND | 10 | 0.02 | 0.24 | USD
42 | Resistors | Bourns | CR0603-JW-104ELF | 0603 (1608 Metric) | RES SMD 100K OHM 5% 1/10W 0603 | 8 | Digi-Key | CR0603-JW-104ELFCT-ND | 80 | 0.01 | 0.67 | USD
43 | Resistors | Panasonic | ERJ3EKF7502V | 0603 (1608 Metric) | RES SMD 75K OHM 1% 1/10W 0603 | 6 | Digi-Key | P75.0KHCT-ND | 60 | 0.07 | 3.90 | USD
44 | Resistors | Yageo | RC0805FR-0710KL | 0805 (2012 Metric) | RES SMD 10K OHM 1% 1/8W 0805 | 2 | Digi-Key | 311-10.0KCRCT-ND | 20 | 0.04 | 0.84 | USD
45 | Resistors | Stackpole Electronics | RNCF0603BTE213K | 0603 (1608 Metric) | RES SMD 213K OHM 0.1% 1/10W 0603 | 1 | Digi-Key | RNCF0603BTE213KCT-ND | 10 | 0.30 | 2.99 | USD
46 | Resistors | Stackpole Electronics | RMCF0603FT68K1 | 0603 (1608 Metric) | RES SMD 68.1K OHM 1% 1/10W 0603 | 1 | Digi-Key | RMCF0603FT68K1CT-ND | 10 | 0.02 | 0.17 | USD
47 | Resis1ors | Samsung | RU1608FR100CS | 0603 (1608 Metric) | RES SMD 0.1 OHM 1% 1/4W 0603 | 4 | Digi-Key | 1276-6155-1-ND | 40 | 0.20 | 8.06 | USD
48 | Resistors | Yageo | RC0603JR-0713KL | 0603 (1608 Metric) | RES SMD 13K OHM 5% 1/10W 0603 | 4 | Digi-Key | 311-13KGRCT-ND | 40 | 0.02 | 0.80 | USD
49 | Resisrors | Yageo | RT0805FRE071ML | 0805 (2012 Metric) | RES SMD 1M OHM 1% 1/8W 0805 | 2 | Digi-Key | YAG3361DKR-ND | 20 | 0.09 | 1.86 | USD
50 | Resistors | TE Connectivity | CRGCQ0603F330K | 0603 (1608 Metric) | RES SMD 330K OHM 1% 1/10W 0603 | 2 | Digi-Key | A129718CT-ND | 20 | 0.03 | 0.62 | USD
51 | Switches | ITT C&K | KMR631NGULCLFS | - | SWITCH TACTILE SPST-NO 50MA 32V | 1 | Digi-Key | CKN10685DKR-ND | 10 | 0.34 | 3.43 | USD
52 | Integrated Circuits | Texas Instruments | INA260AIPWR | 16-TSSOP | IC MONITOR PWR/CURR 16TSSOP | 3 | Digi-Key | 296-47777-1-ND | 30 | 4.08 | 122.31 | USD
53 | Integrated Circuits | STMicroelectronics | SPV1040TTR | 8-TSSOP | IC SOLAR BATTERY CHARGER 8TSSOP | 3 | Digi-Key | 497-11288-1-ND | 30 | 2.92 | 87.66 | USD
54 | Integrated Circuits | Analog Devices / Linear Technology | LTC4352IMS#PBF | 12-MSOP | IC OR CTRLR N+1 12MSOP | 1 | Digi-Key | LTC4352IMS#PBF-ND | 10 | 7.04 | 70.40 | USD
55 | Integrated Circuits | Texas Instruments | BQ27441DRZR-G1A | 12-SON | IC BATT FUEL GAUGE LI-ION 12SON | 1 | Digi-Key | 296-39941-6-ND | 10 | 2.35 | 23.53 | USD
56 | Integrated Circuits | Texas Instruments | TPS2557DRBT | 8-SON | IC PWR DIST SWITCH ADJ 8SON | 2 | Digi-Key | 296-25432-1-ND | 20 | 2.21 | 44.22 | USD
57 | Integrated Circuits | Texas Instruments | TPS2551QDBVRQ1 | SOT23-6 | IC POWER-DIST SWITCH ADJ SOT23-6 | 6 | Digi-Key | 296-23692-1-ND | 60 | 2.42 | 145.02 | USD
58 | Integrated Circuits | Texas Instruments | TPS63070RNMT | 15-VQFN | IC REG BCK BST ADJ 2A 15VQFN | 1 | Digi-Key | 296-44764-1-ND | 10 | 2.48 | 24.81 | USD
59 | Integrated Circuits | Microchip | MCP1252-33X50I/MS | 8-MSOP | IC REG SWITCHD CAP PROG 8MSOP | 1 | Digi-Key | MCP1252-33X50I/MS-ND | 10 | 1.41 | 14.10 | USD
60 | Integrated Circuits | Texas Instruments | INA169NA/3K | SOT23-5 | IC CURRENT MONITOR 0.5% SOT23-5 | 4 | Digi-Key | 296-26063-6-ND | 40 | 2.04 | 81.68 | USD
61 | Integrated Circuits | Microchip / Atmel | ATMEGA328P-AUR | 32-TQFP | IC MCU 8BIT 32KB FLASH 32TQFP | 1 | Digi-Key | ATMEGA328P-AURCT-ND | 10 | 2.14 | 21.40 | USD
62 | Integrated Circuits | FTDI | FT232RL-REEL | 28-SSOP | IC USB FS SERIAL UART 28-SSOP | 1 | Digi-Key | 768-1007-6-ND | 10 | 4.05 | 40.50 | USD
63 | Crystals | Abracon | ABM7-8.000MHZ-D2Y-T | - | CRYSTAL 8.0000MHZ 18PF SMD | 1 | Digi-Key | 535-9831-6-ND | 10 | 0.63 | 6.33 | USD
 |  |  |  |  |  | 209 |  |  | 2090 |  | 1204.59
Approved: |  |  |  | Notes:
 |  |  |  |  |  | 10 | pcs: | Total |  | 1204.59 | USD
 |  |  |  |  |  |  |  | Price for 1pcs: |  | 120.46 | USD

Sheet: Project Information
Project Full Path | C:\Users\josea\Desktop\2018\UVG 2018\Research\CubeSat\Hardware\Altium\Flight Boards\PT-PWR-EPS-002_v1\PT-PWR-EPS-002_v1.PrjPcb
Project Filename | PT-PWR-EPS-002_v1.PrjPcb
Variant Name | None
Data-Source Filename | PT-PWR-EPS-002_v1.PrjPcb
Data-Source Full Path | C:\Users\josea\Desktop\2018\UVG 2018\Research\CubeSat\Hardware\Altium\Flight Boards\PT-PWR-EPS-002_v1\PT-PWR-EPS-002_v1.PrjPcb
Title | PT-PWR-EPS-002_v1 BOM Purchasing for Project [PT-PWR-EPS-002_v1.PrjPcb] (No PCB Document Selected)
Total Quantity | 216
Report Time | 4:23 p. m.
Report Date | 13/06/2019
Report Date & Tine | 13/06/2019 4:23 p. m.
Output Name | PT-PWR-EPS-002_v1 BOM Purchasing
Output Type | BOM_PartType
Output Generator Name | BOM
Output Generator Description | Bill of Materials

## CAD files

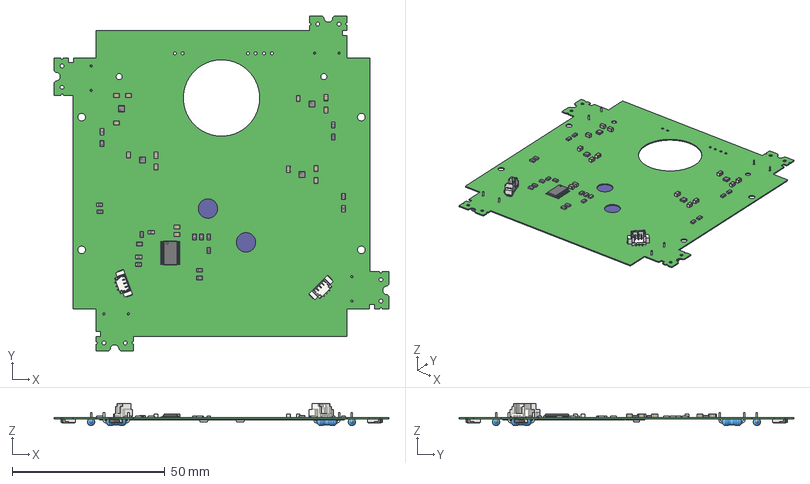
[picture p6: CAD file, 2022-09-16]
ADM/src/PT-MIS-PCB-004_v1.step
109.7 x 109.7 x 7.30 mm
Board
0805_resistor x 19
PT-PWR-SCL-001_SOLAR_CELL
PT-PWR-SCL-001_INTERCONNECTOR x 3
PT-PWR-SCL-001_COVER_GLASS
PT-PWR-SCL-001_EXTERNAL_DIODE
User_Library-SON8-2x2mm-1 x 4
User_Library-TSSOP-24__X2_041A043E0440043F04430441_X0_
User_Library-TSSOP-24__X2_041C04350442043A0430_X0_
User_Library-TSSOP-24__X2_041D043E0436043A0430_X0_ x 12
0805_cap x 14
PT-ADC-SNS-002-PHOTODIODES x 2
sw-131-e18cs-pc-1 x 4
sw-131-e18lv3-sk-1 x 4
sw-131-e18fm4-sk-1 x 4
sw-131-e18ts-f-sk-1 x 4
sw-131-e18ts-f-sk-1_1 x 4
sw-131-e18ts-f-sk-1_2 x 4
sw-131-e18ts-f-sk-1_3 x 4
CONN_HEADER_3POS_1.25MM_VERT_SMD533980371 x 2
MFR-50_Yageo_Resistor x 4
Free-Models

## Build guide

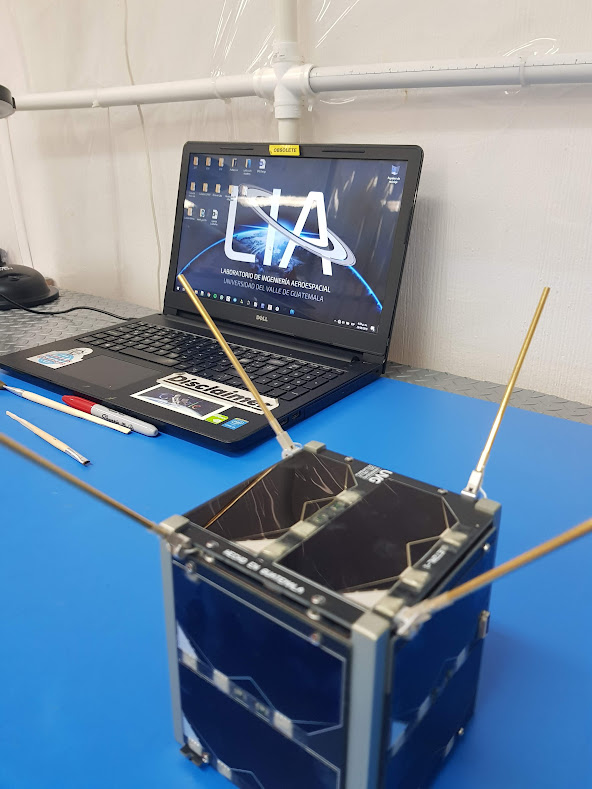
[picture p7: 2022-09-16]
ADM/media/assembled_satellite_antennas_deployed.jpg

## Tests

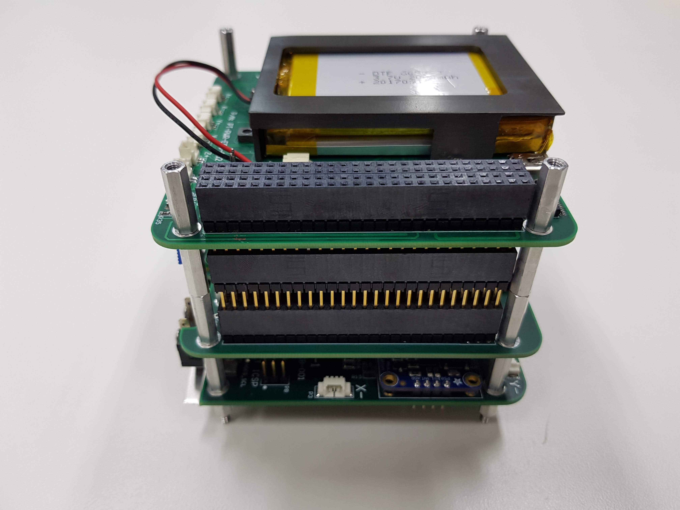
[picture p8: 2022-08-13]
ADCS/media/adcs-payload-eps-integration-test-2.jpg

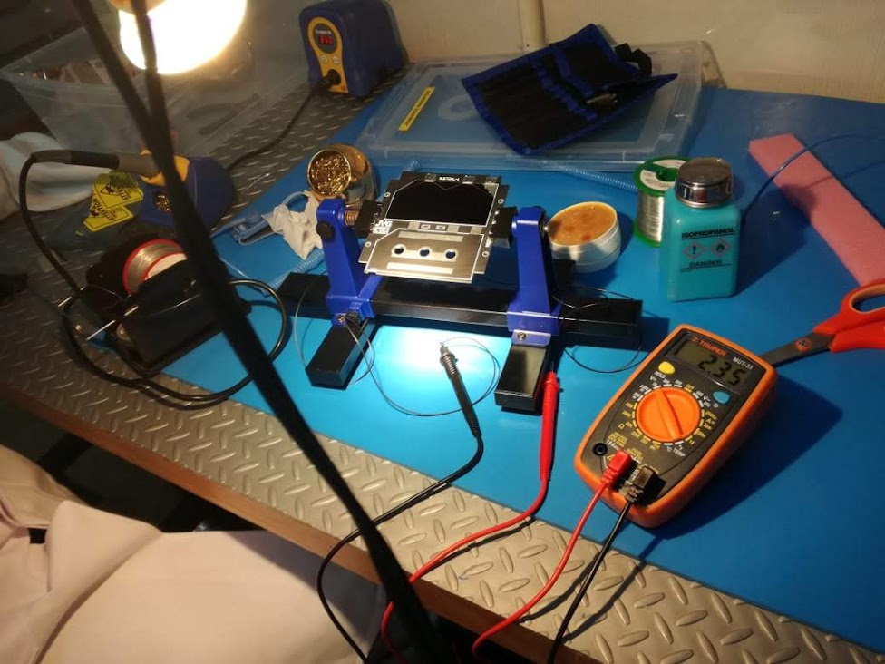
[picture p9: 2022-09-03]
EPS/media/solar_cell_soldering_and_operation_engineering_test.jpg

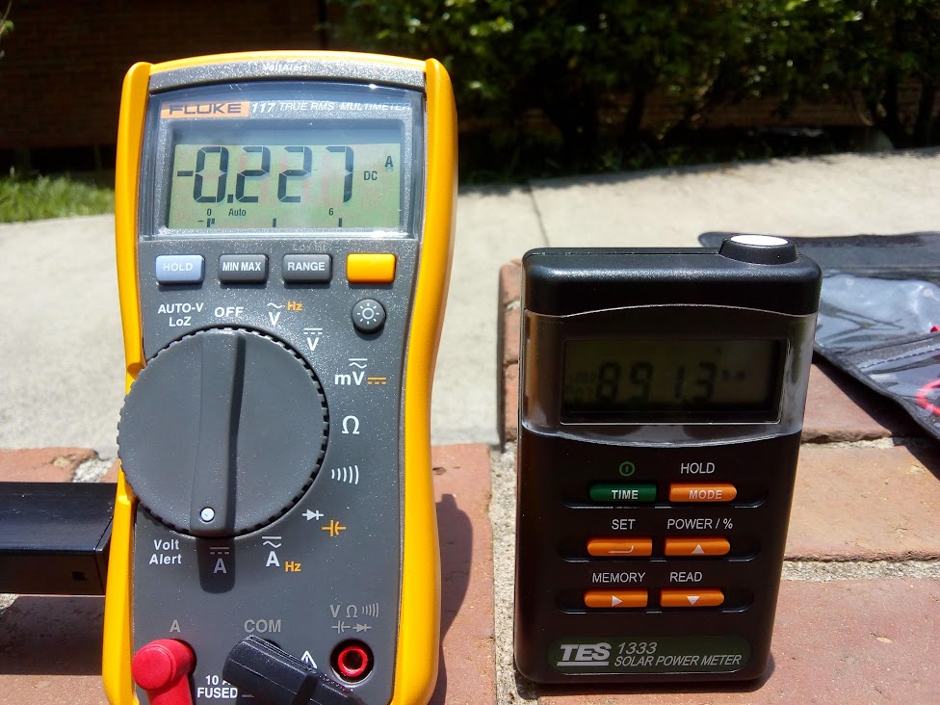
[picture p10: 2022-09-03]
EPS/media/battery_charging_with_solar_panel_engineering_model_test.jpg

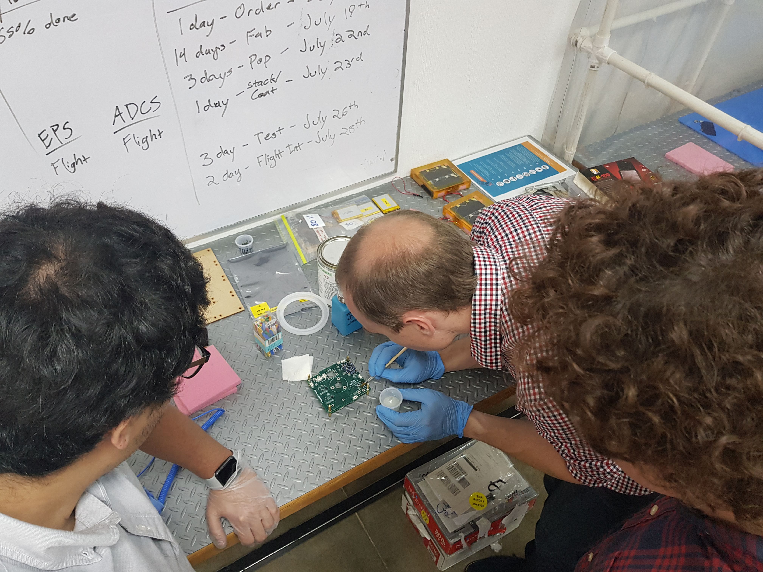
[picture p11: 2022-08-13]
ADCS/media/adcs-engineering-model-arathane-coating-test.jpg

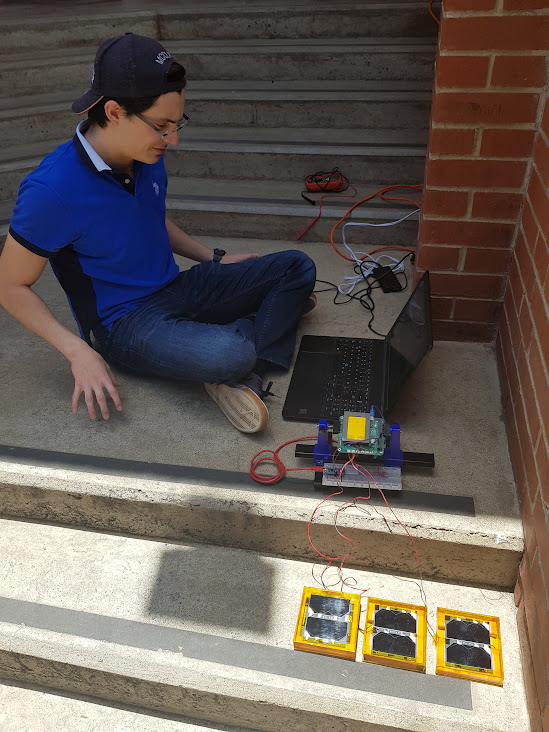
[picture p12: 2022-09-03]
EPS/media/eps_engineering_model_tests_2.jpg

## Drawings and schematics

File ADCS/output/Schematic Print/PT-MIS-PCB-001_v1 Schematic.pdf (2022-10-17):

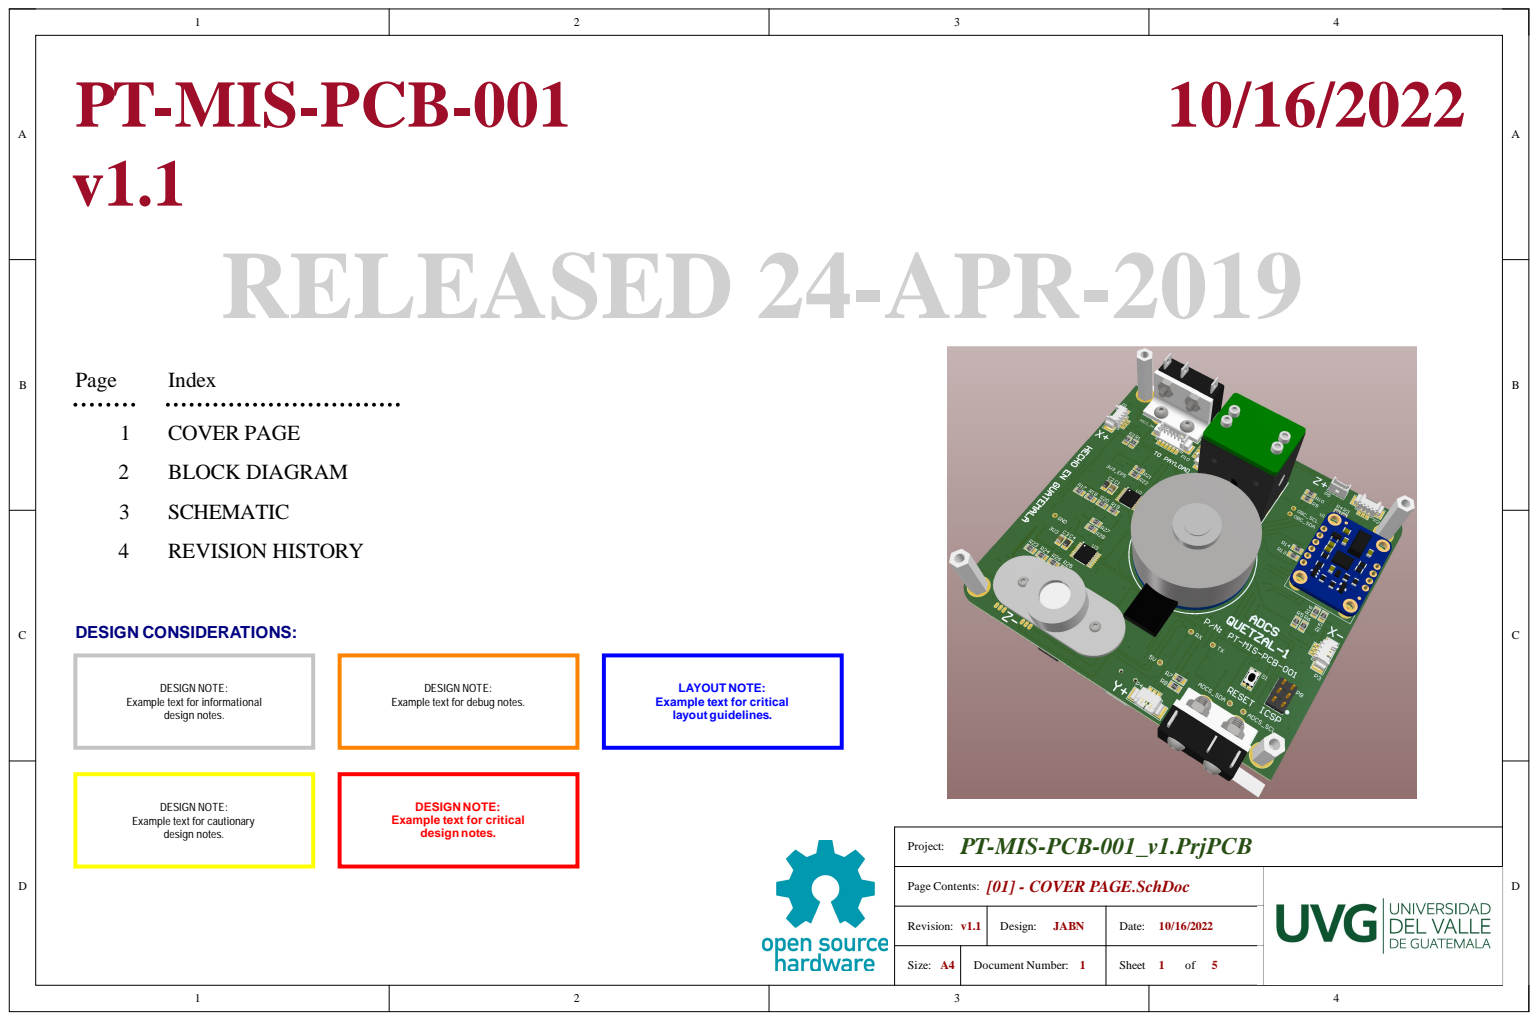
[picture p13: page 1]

DESIGN NOTE:
Example text for debug notes.

LAYOUT NOTE:
Example text for critical
layout guidelines.

Example text for informational

Example text for cautionary
design notes.

PT-MIS-PCB-001_v1.PrjPCB

Page Contents: [01] - COVER PAGE.SchDoc

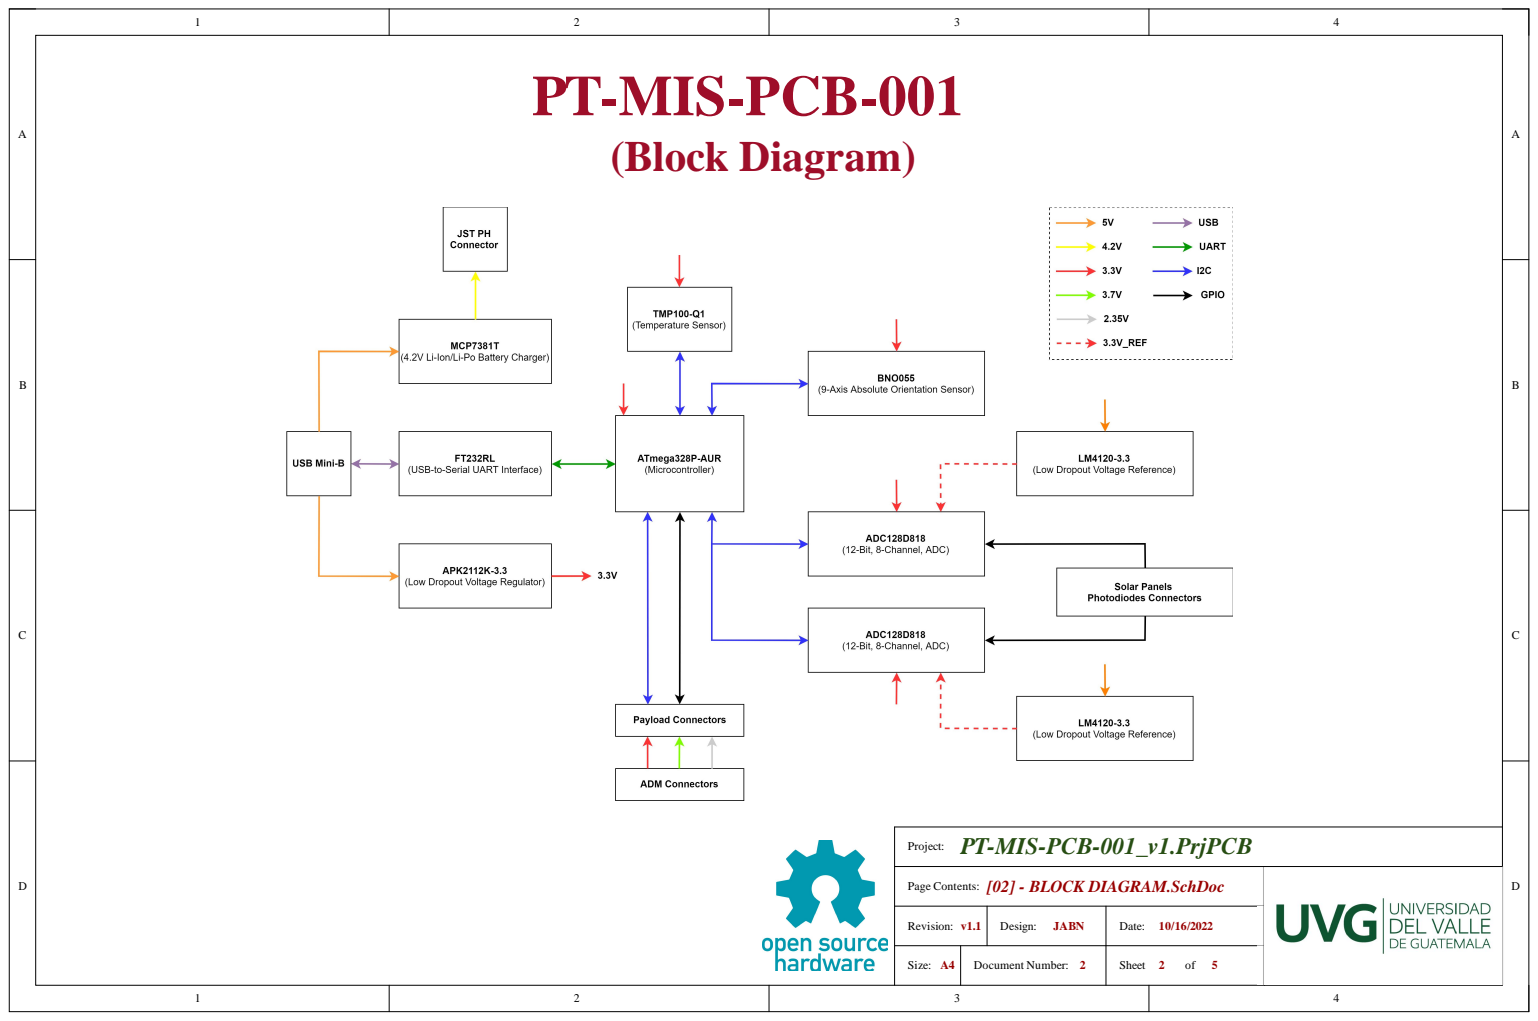
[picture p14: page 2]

PT-MIS-PCB-001_v1.PrjPCB

Page Contents: [02] - BLOCK DIAGRAM.SchDoc

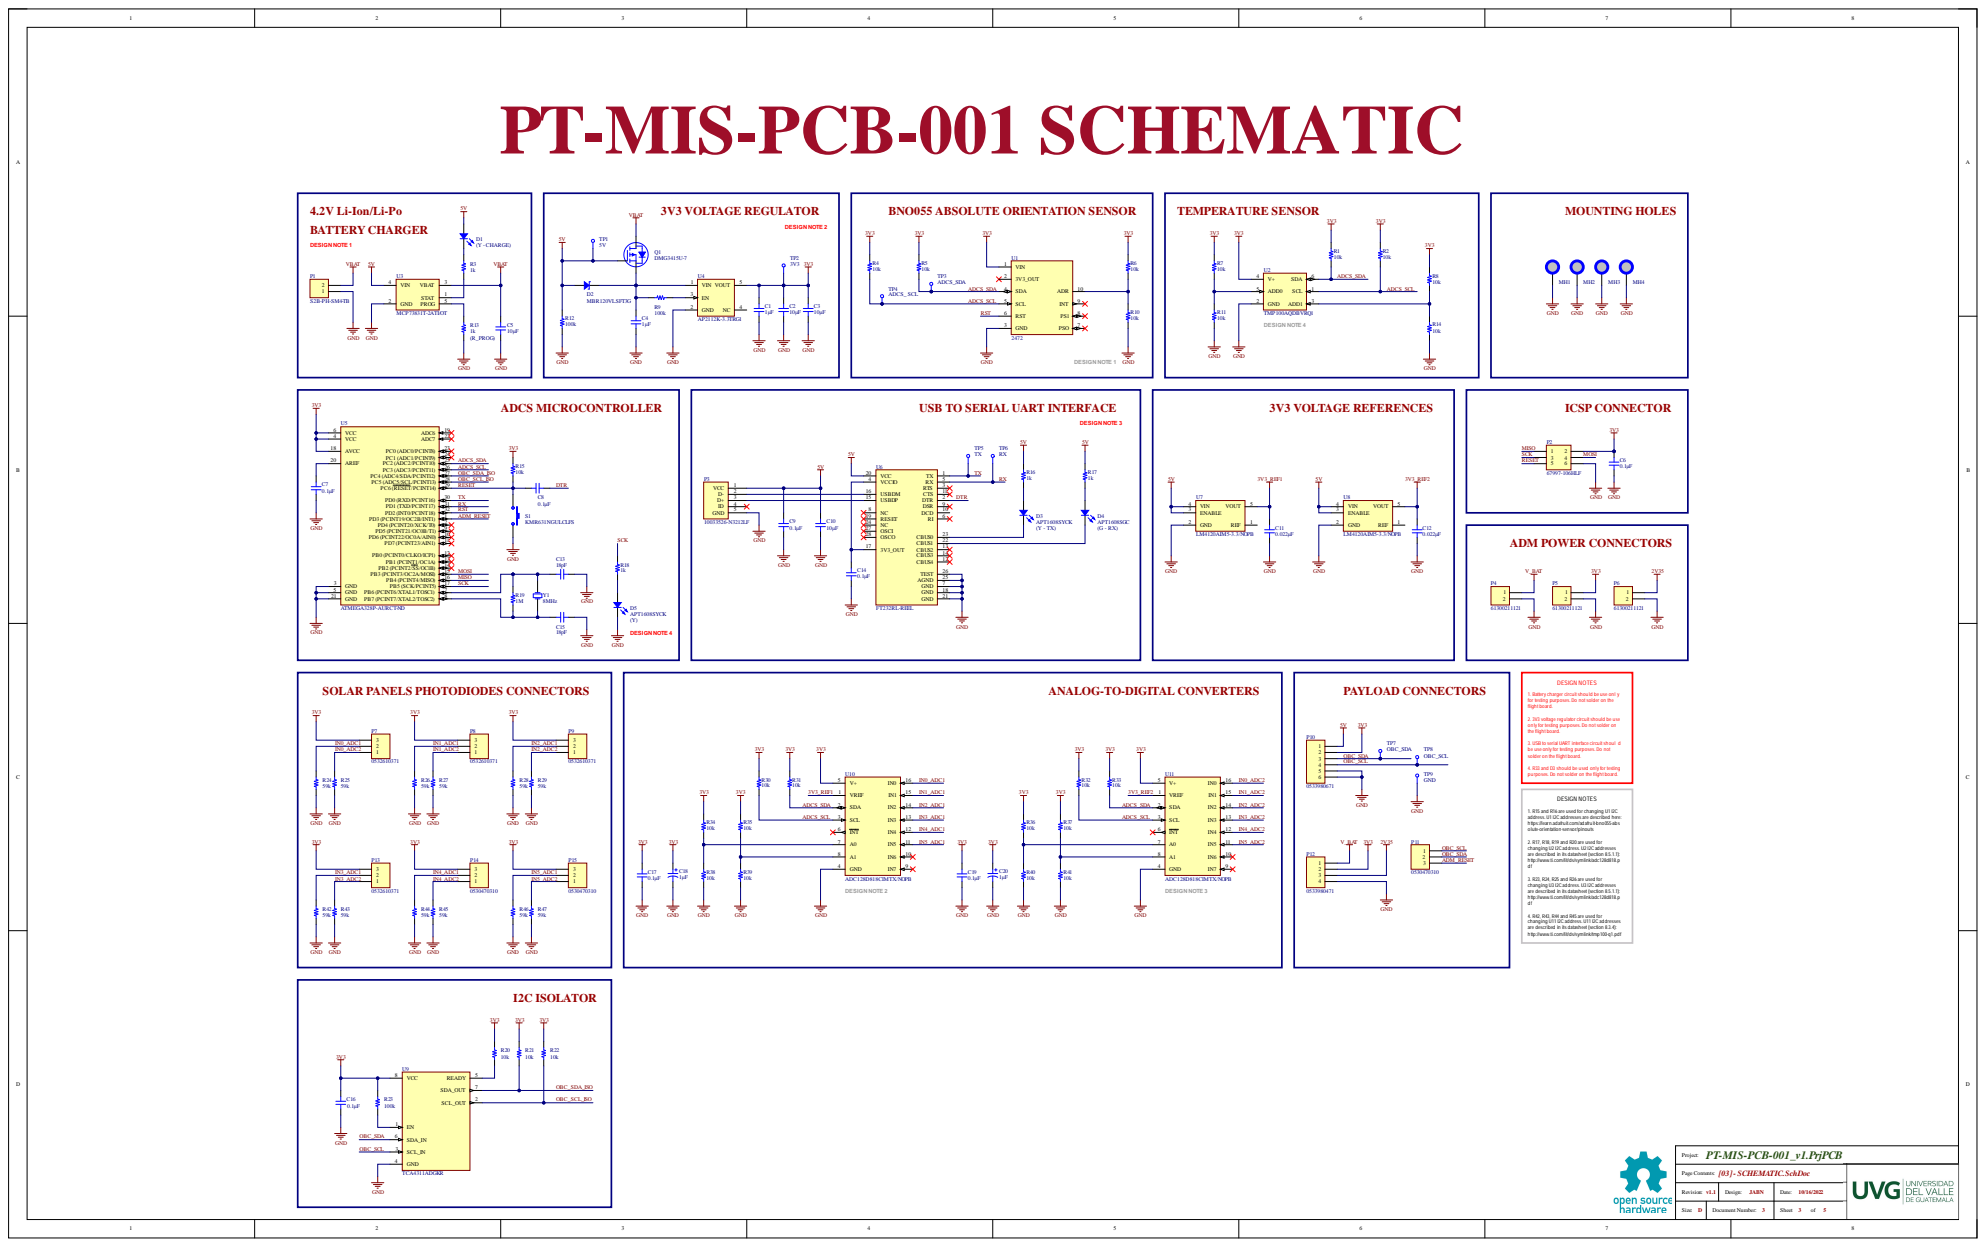
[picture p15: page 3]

PT-MIS-PCB-001 SCHEMATIC

4.2V Li-Ion/Li-Po
BATTERY CHARGER

1. Battery charger circuit should be use only
for testing purposes. Do not solder on the
flight board.

2. 3V3 voltage regulator circuit should be use
only for testing purposes. Do not solder on
the flight board.

3. USB to serial UART interface circuit should
be use only for testing purposes. Do not
solder on the flight board.

4. R33 and D3 should be used only for testing
purposes. Do not solder on the flight board.

1. R15 and R16 are used for changing U1 I2C
address. U1 I2C addresses are described here:
https://learn.adafruit.com/adafruit-bno055-abs
olute-orientation-sensor/pinouts

2. R17, R18, R19 and R20 are used for
changing U2 I2C address. U2 I2C addresses
are described in its datasheet (section 8.5.1.1):
http://www.ti.com/lit/ds/symlink/adc128d818.p

3. R23, R24, R25 and R26 are used for
changing U3 I2C address. U3 I2C addresses

4. R42, R43, R44 and R45 are used for
changing U11 I2C address. U11 I2C addresses
are described in its datasheet (section 8.3.4):
http://www.ti.com/lit/ds/symlink/tmp100-q1.pdf

PT-MIS-PCB-001_v1.PrjPCB

Page Contents: [03]- SCHEMATIC.SchDoc

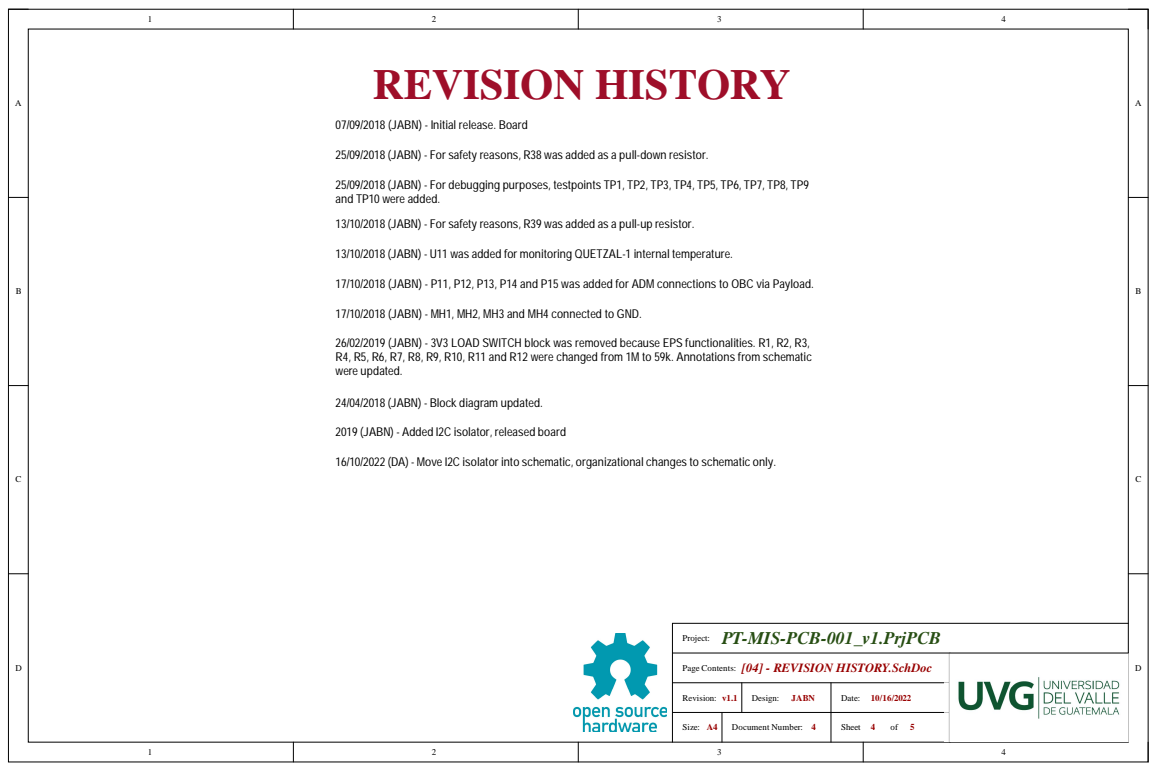
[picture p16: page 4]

07/09/2018 (JABN) - Initial release. Board

25/09/2018 (JABN) - For safety reasons, R38 was added as a pull-down resistor.

25/09/2018 (JABN) - For debugging purposes, testpoints TP1, TP2, TP3, TP4, TP5, TP6, TP7, TP8, TP9
and TP10 were added.

13/10/2018 (JABN) - For safety reasons, R39 was added as a pull-up resistor.

13/10/2018 (JABN) - U11 was added for monitoring QUETZAL-1 internal temperature.

17/10/2018 (JABN) - P11, P12, P13, P14 and P15 was added for ADM connections to OBC via Payload.

17/10/2018 (JABN) - MH1, MH2, MH3 and MH4 connected to GND.

26/02/2019 (JABN) - 3V3 LOAD SWITCH block was removed because EPS functionalities. R1, R2, R3,
R4, R5, R6, R7, R8, R9, R10, R11 and R12 were changed from 1M to 59k. Annotations from schematic
were updated.

24/04/2018 (JABN) - Block diagram updated.

2019 (JABN) - Added I2C isolator, released board

16/10/2022 (DA) - Move I2C isolator into schematic, organizational changes to schematic only.

PT-MIS-PCB-001_v1.PrjPCB

Page Contents: [04] - REVISION HISTORY.SchDoc

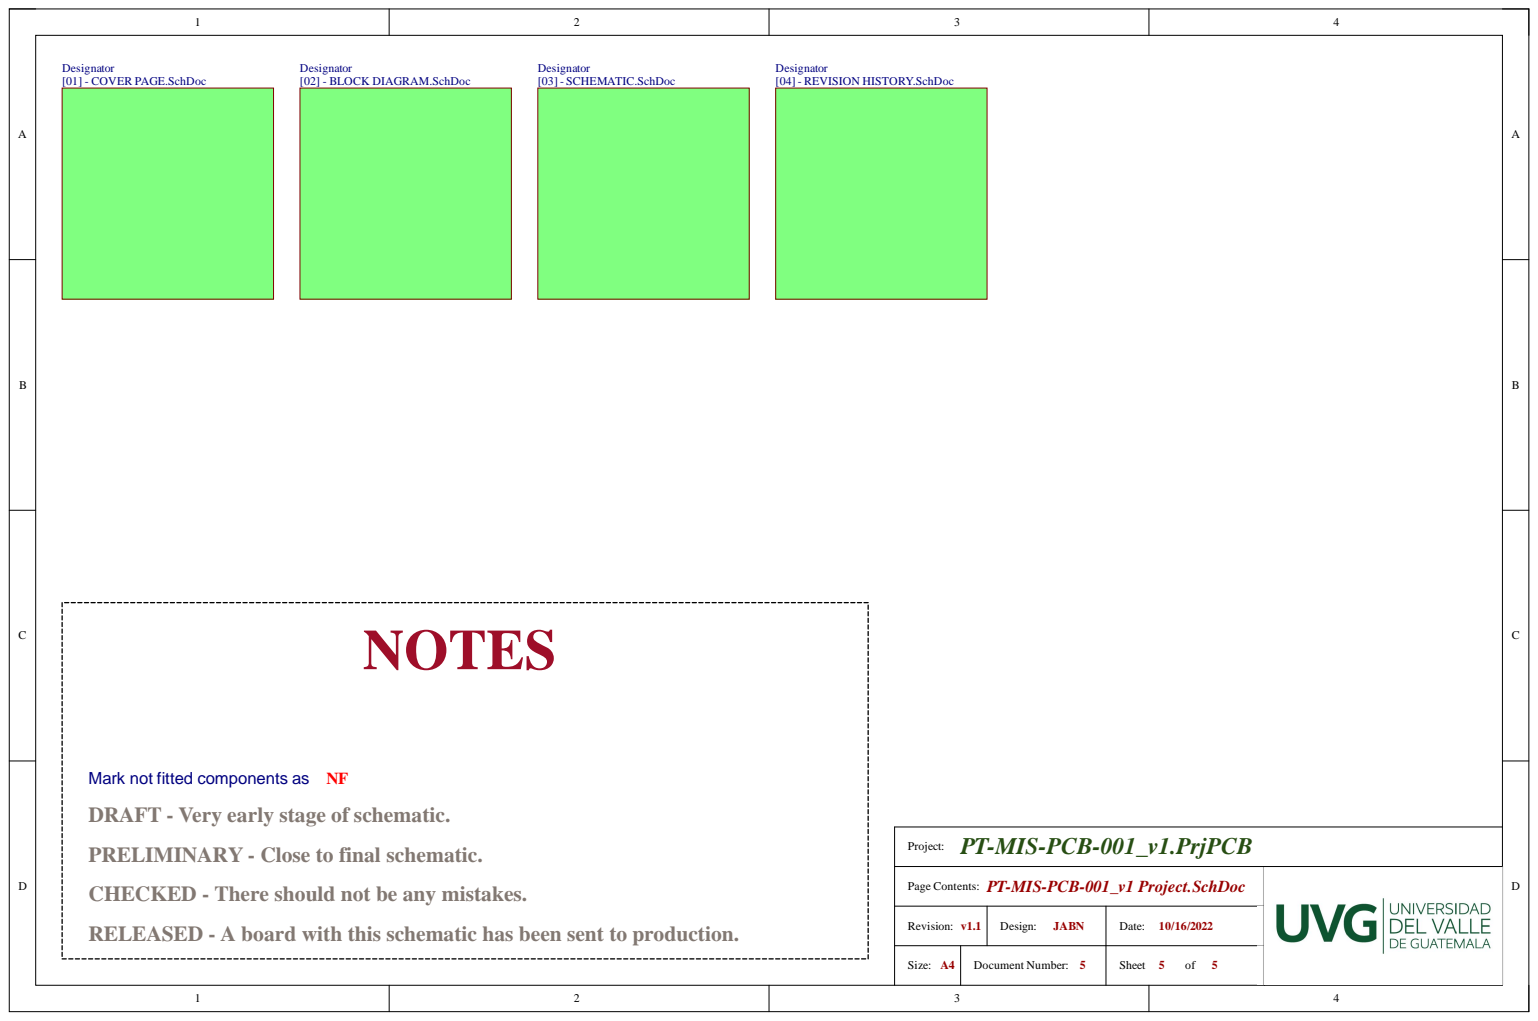
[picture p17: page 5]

Mark not fitted components as NF
DRAFT - Very early stage of schematic.

PT-MIS-PCB-001_v1.PrjPCB

PRELIMINARY - Close to final schematic.

Page Contents: PT-MIS-PCB-001_v1 Project.SchDoc

CHECKED - There should not be any mistakes.

RELEASED - A board with this schematic has been sent to production.

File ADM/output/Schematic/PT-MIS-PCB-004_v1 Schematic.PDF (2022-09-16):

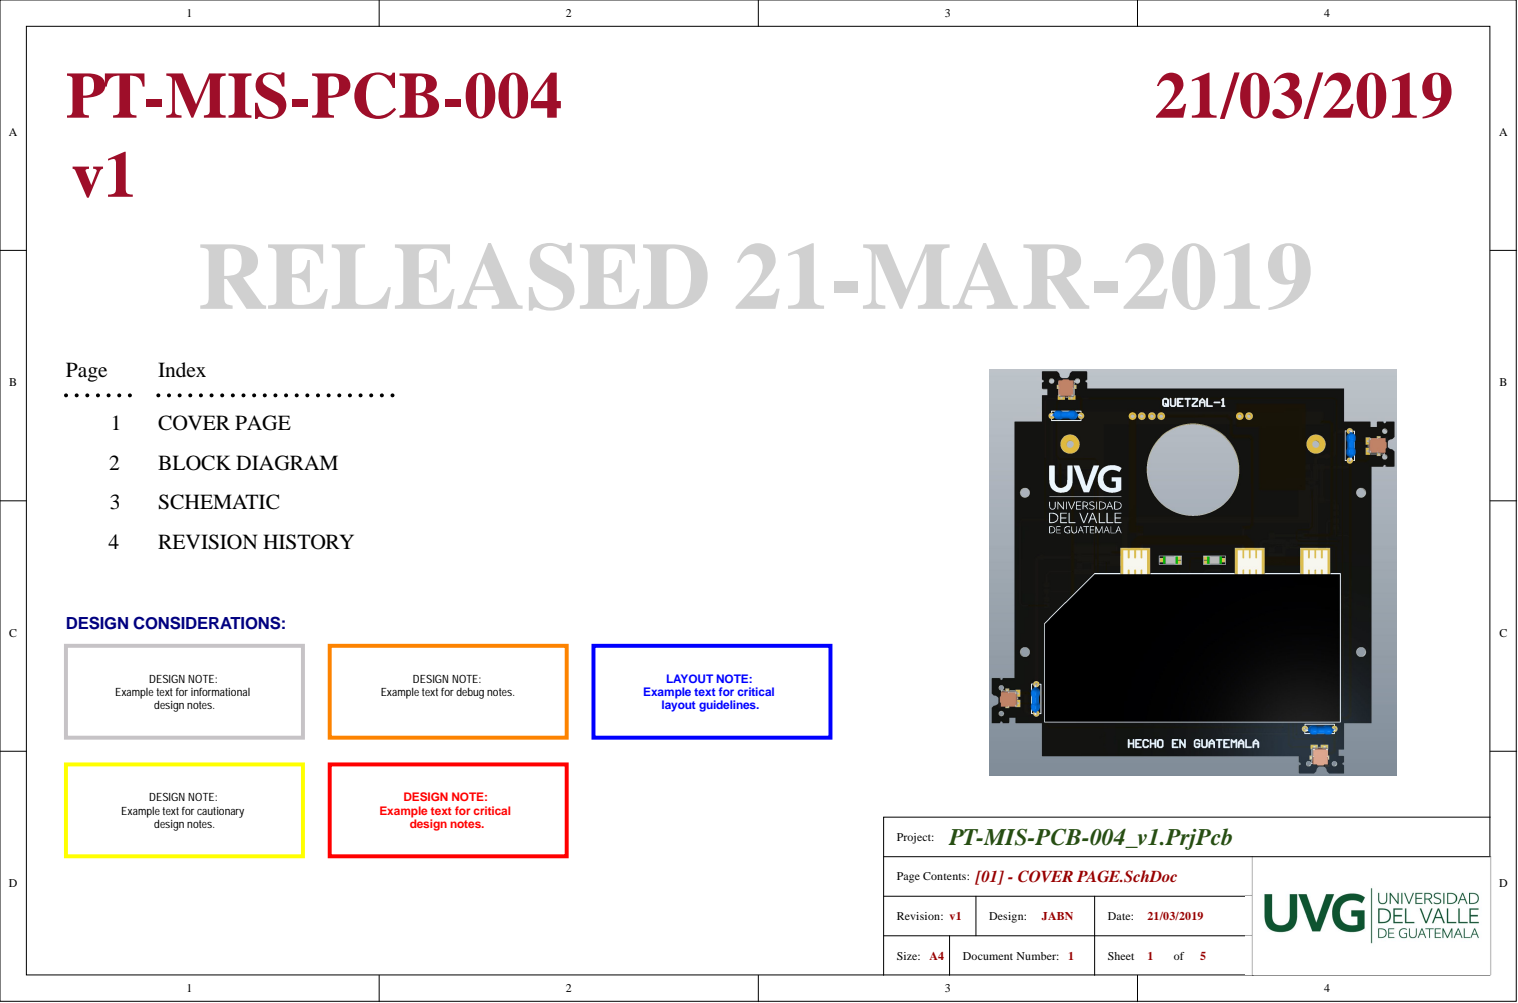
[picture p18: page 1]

DESIGN NOTE:
Example text for debug notes.

LAYOUT NOTE:
Example text for critical
layout guidelines.

Example text for informational

Example text for cautionary
design notes.

PT-MIS-PCB-004_v1.PrjPcb

Page Contents: [01] - COVER PAGE.SchDoc

Revision: v1 | Design: JABN | Date: 21/03/2019

Size: A4 | Document Number: 1 | Sheet 1 5 of

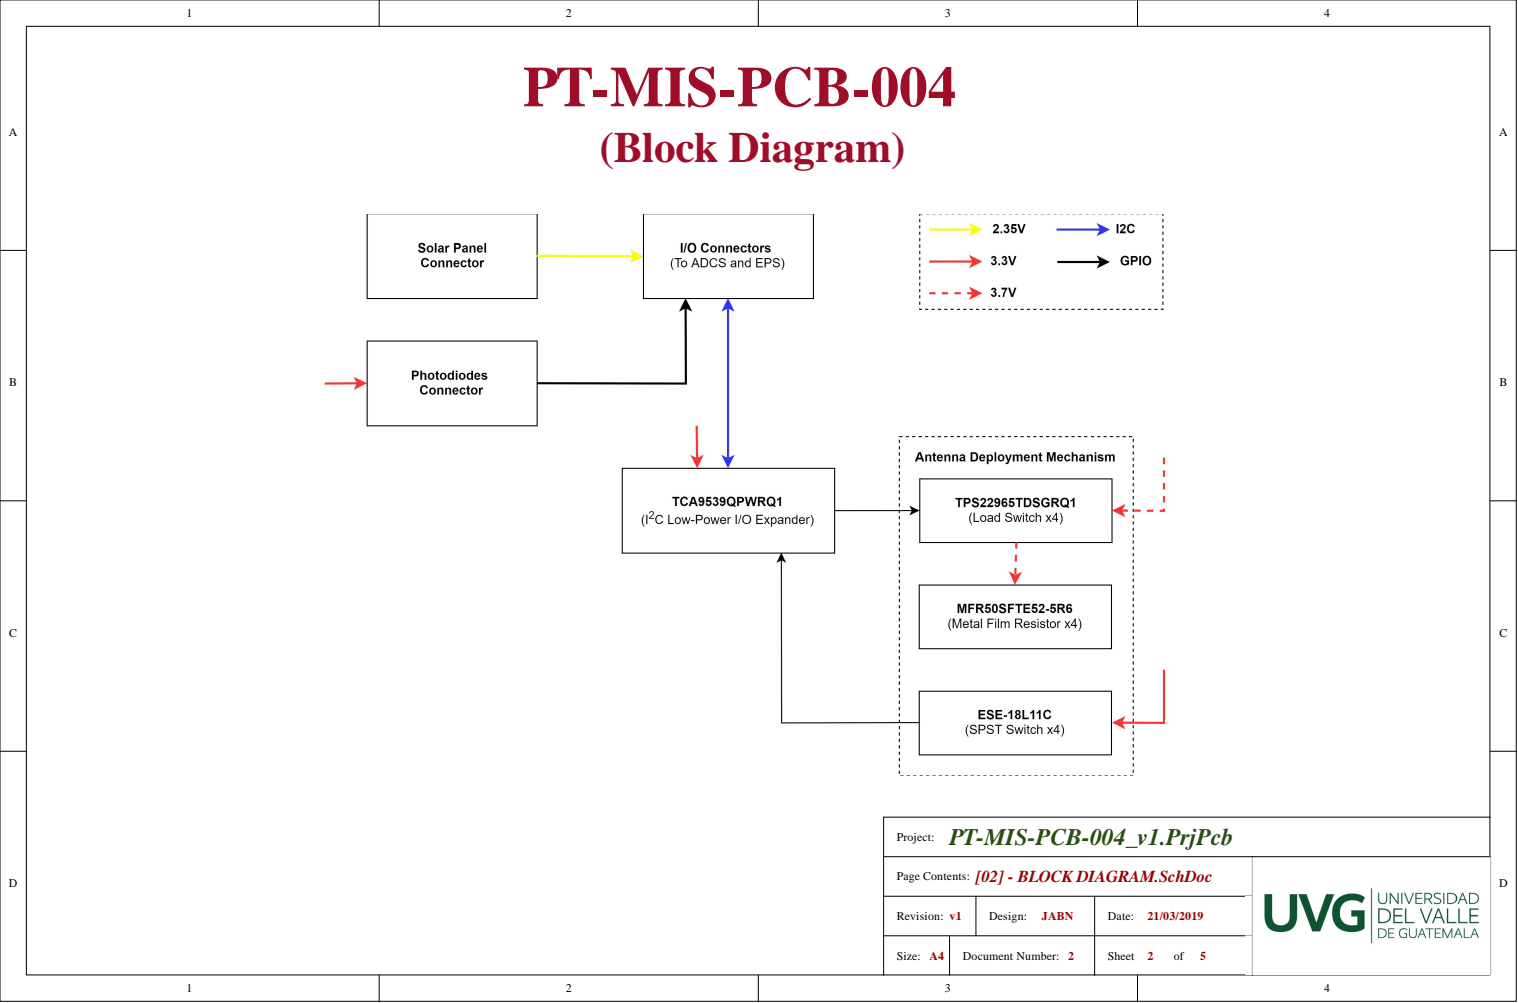
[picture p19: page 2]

PT-MIS-PCB-004_v1.PrjPcb

Page Contents: [02] - BLOCK DIAGRAM.SchDoc

Revision: v1 | Design: JABN | Date: 21/03/2019

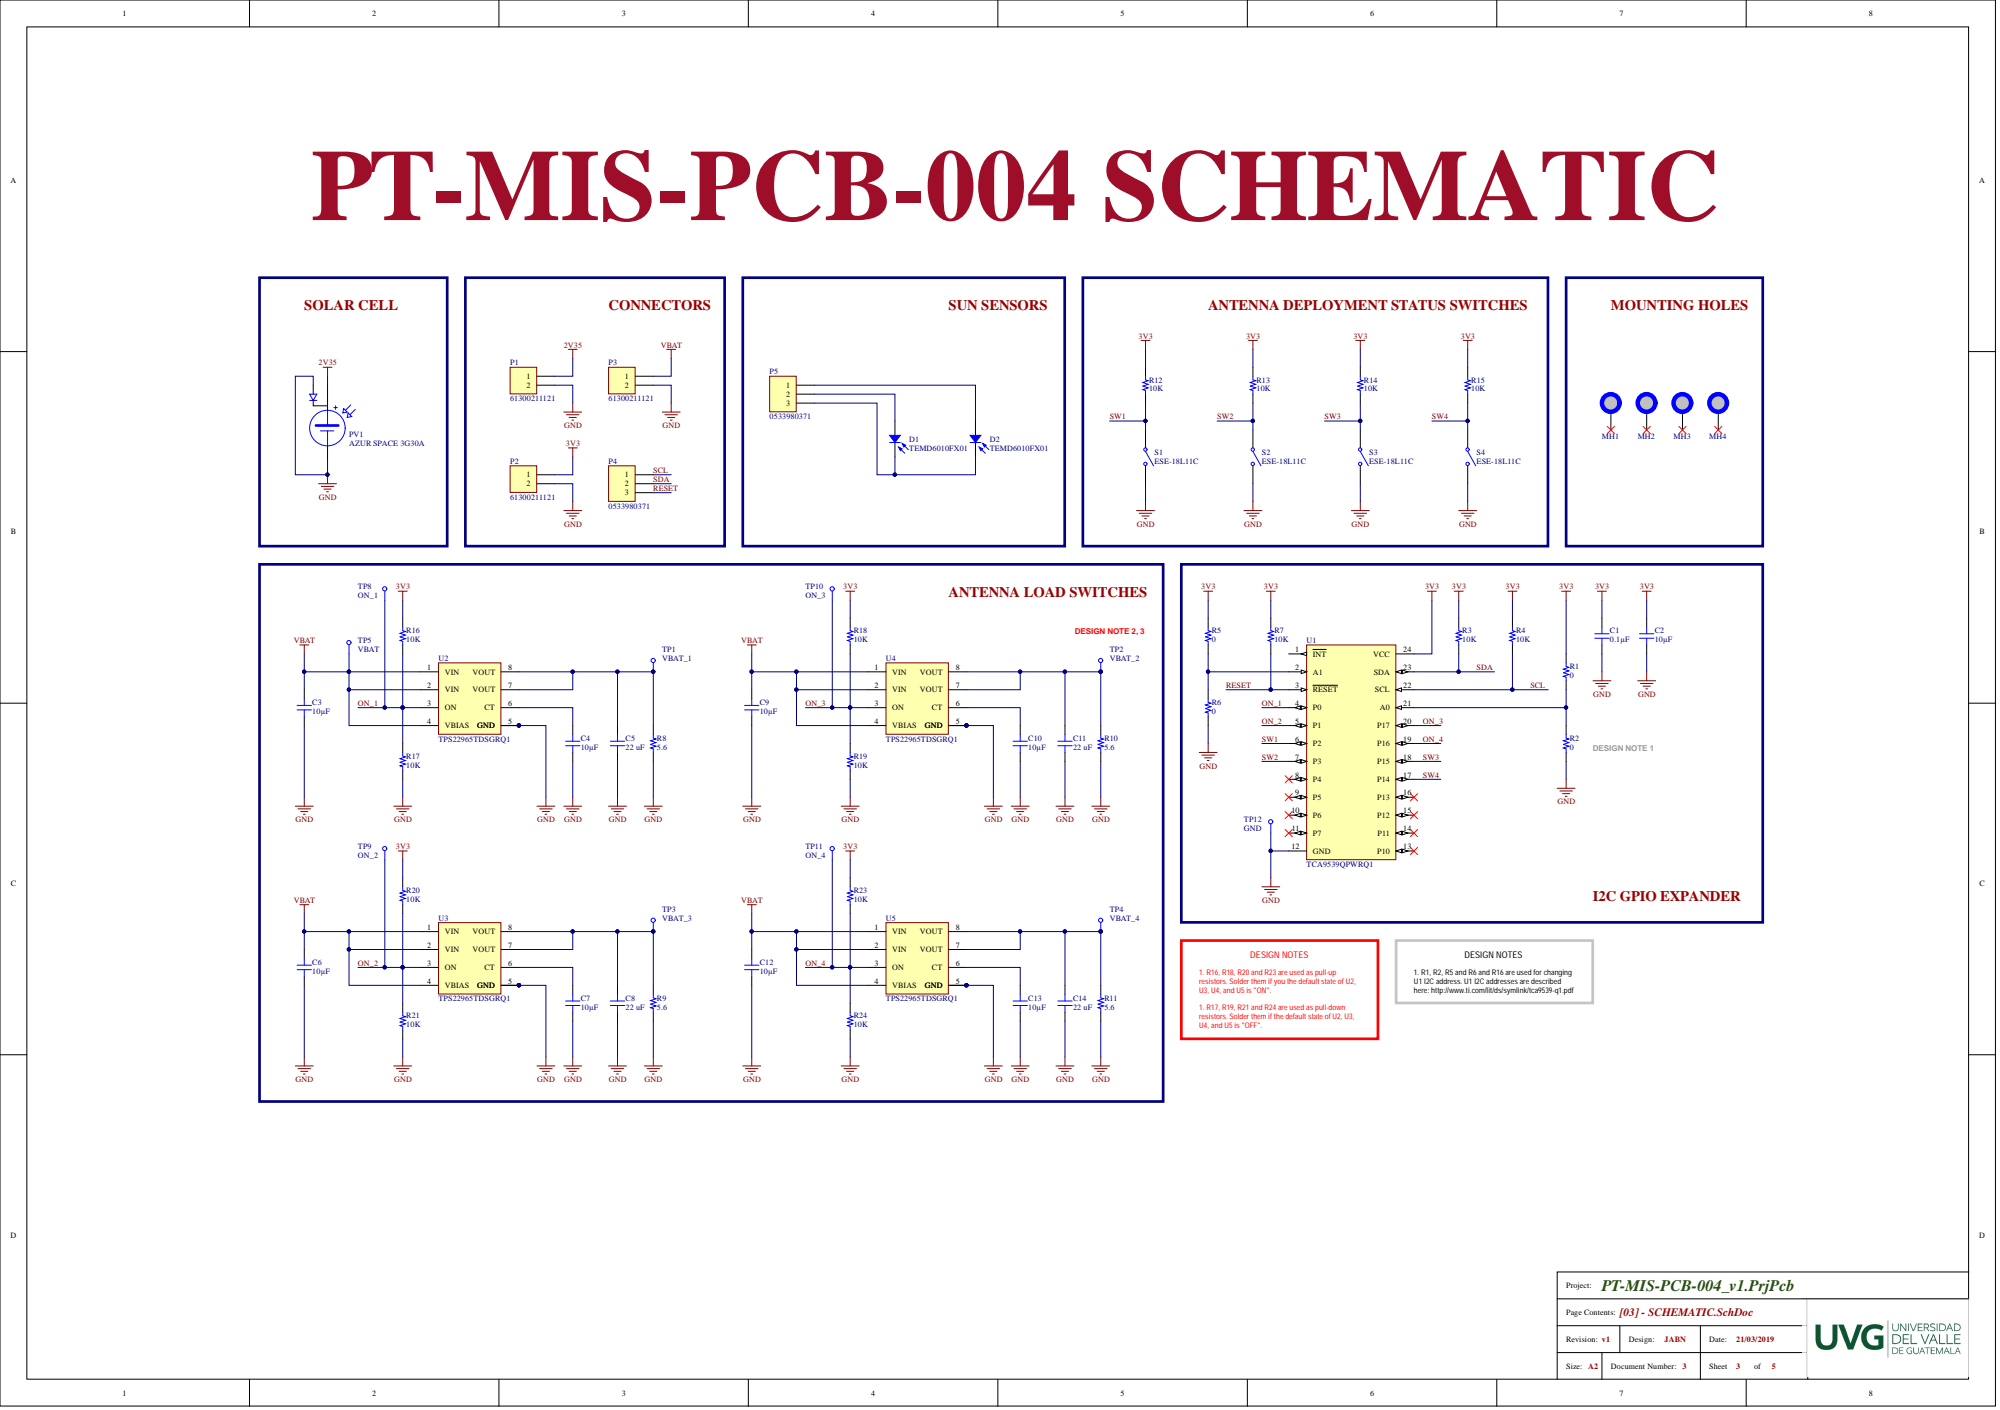
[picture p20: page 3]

PT-MIS-PCB-004 SCHEMATIC

1. R16, R18, R20 and R23 are used as pull-up resistors. Solder them if you the default state of U2, U3, U4, and U5 is "ON". DESIGN NOTES

1. R1, R2, R5 and R6 and R16 are used for changing U1 I2C address. U1 I2C addresses are described

here: http://www.ti.com/lit/ds/symlink/tca9539-q1.pdf

1. R17, R19, R21 and R24 are used as pull-down resistors. Solder them if the default state of U2, U3, U4, and U5 is "OFF".

Page Co n ten t s

Rev i s i o n : | | Date:

Size: A 2 Sheet | D ocumen t N umber: | 3 o f 5

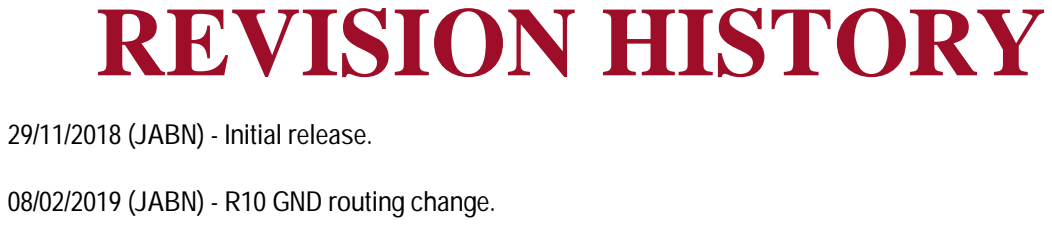
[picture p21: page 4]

08/02/2019 (JABN) - R10 GND routing change.

PT-MIS-PCB-004_v1.PrjPcb

Page Contents: [04] - REVISION HISTORY.SchDoc

Revision: v1 | Design: JABN | Date: 21/03/2019

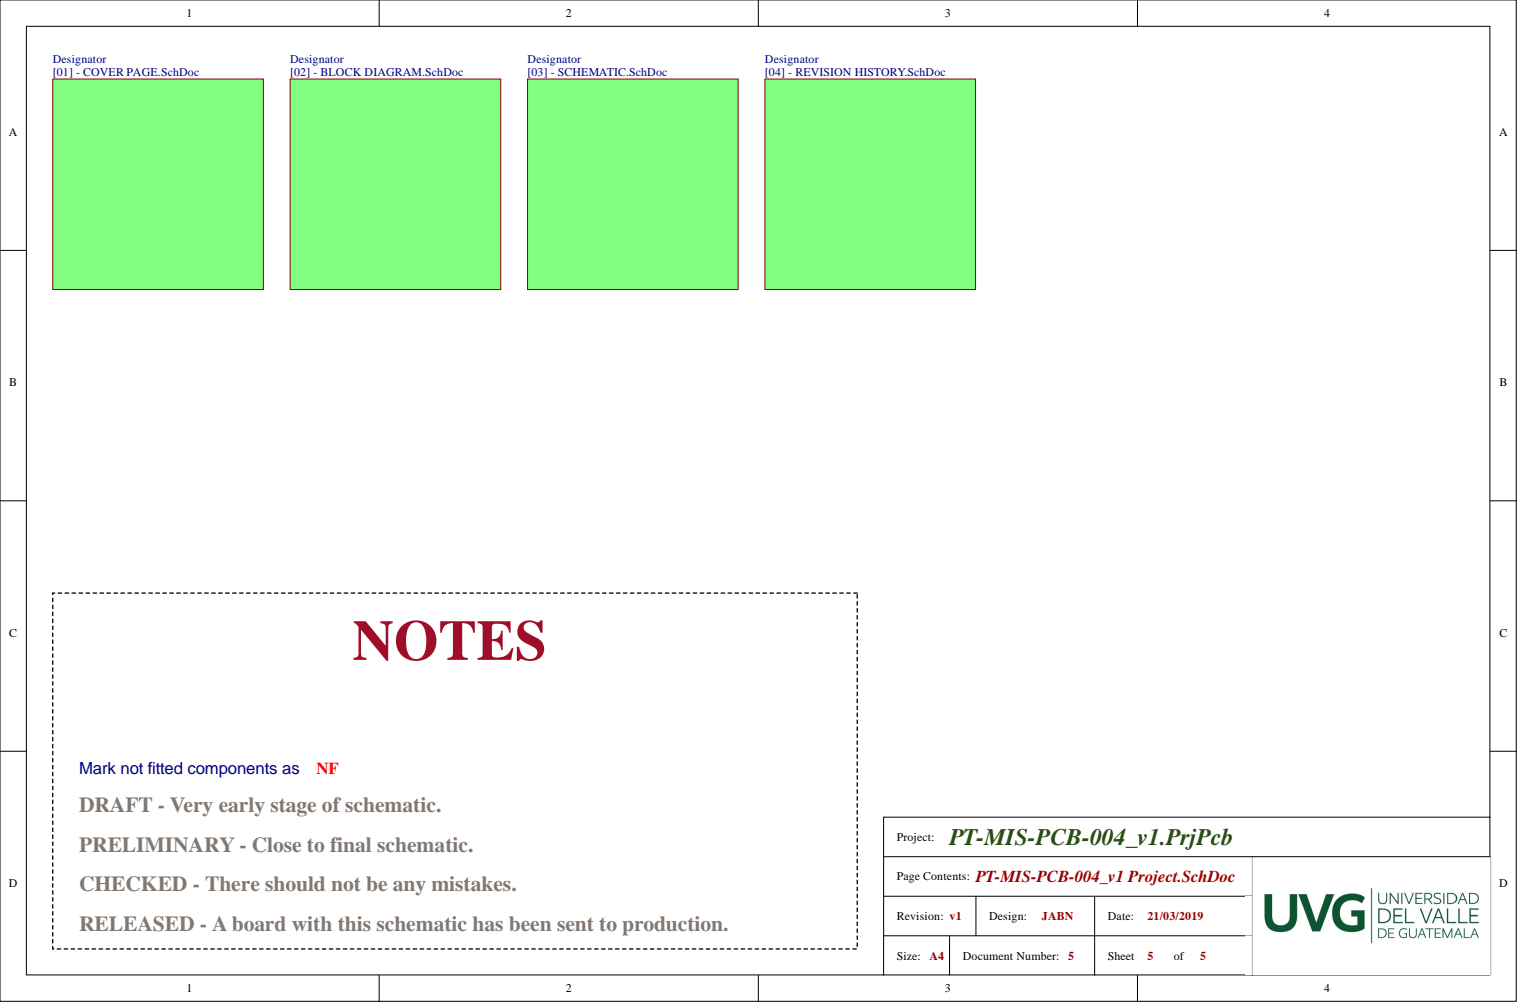
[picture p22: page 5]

Mark not fitted components as NF
DRAFT - Very early stage of schematic.

PT-MIS-PCB-004_v1.PrjPcb

PRELIMINARY - Close to final schematic.

Page Contents: PT-MIS-PCB-004_v1 Project.SchDoc

CHECKED - There should not be any mistakes.

RELEASED - A board with this schematic has been sent to production.

Revision: v1 | Design: JABN | Date: 21/03/2019

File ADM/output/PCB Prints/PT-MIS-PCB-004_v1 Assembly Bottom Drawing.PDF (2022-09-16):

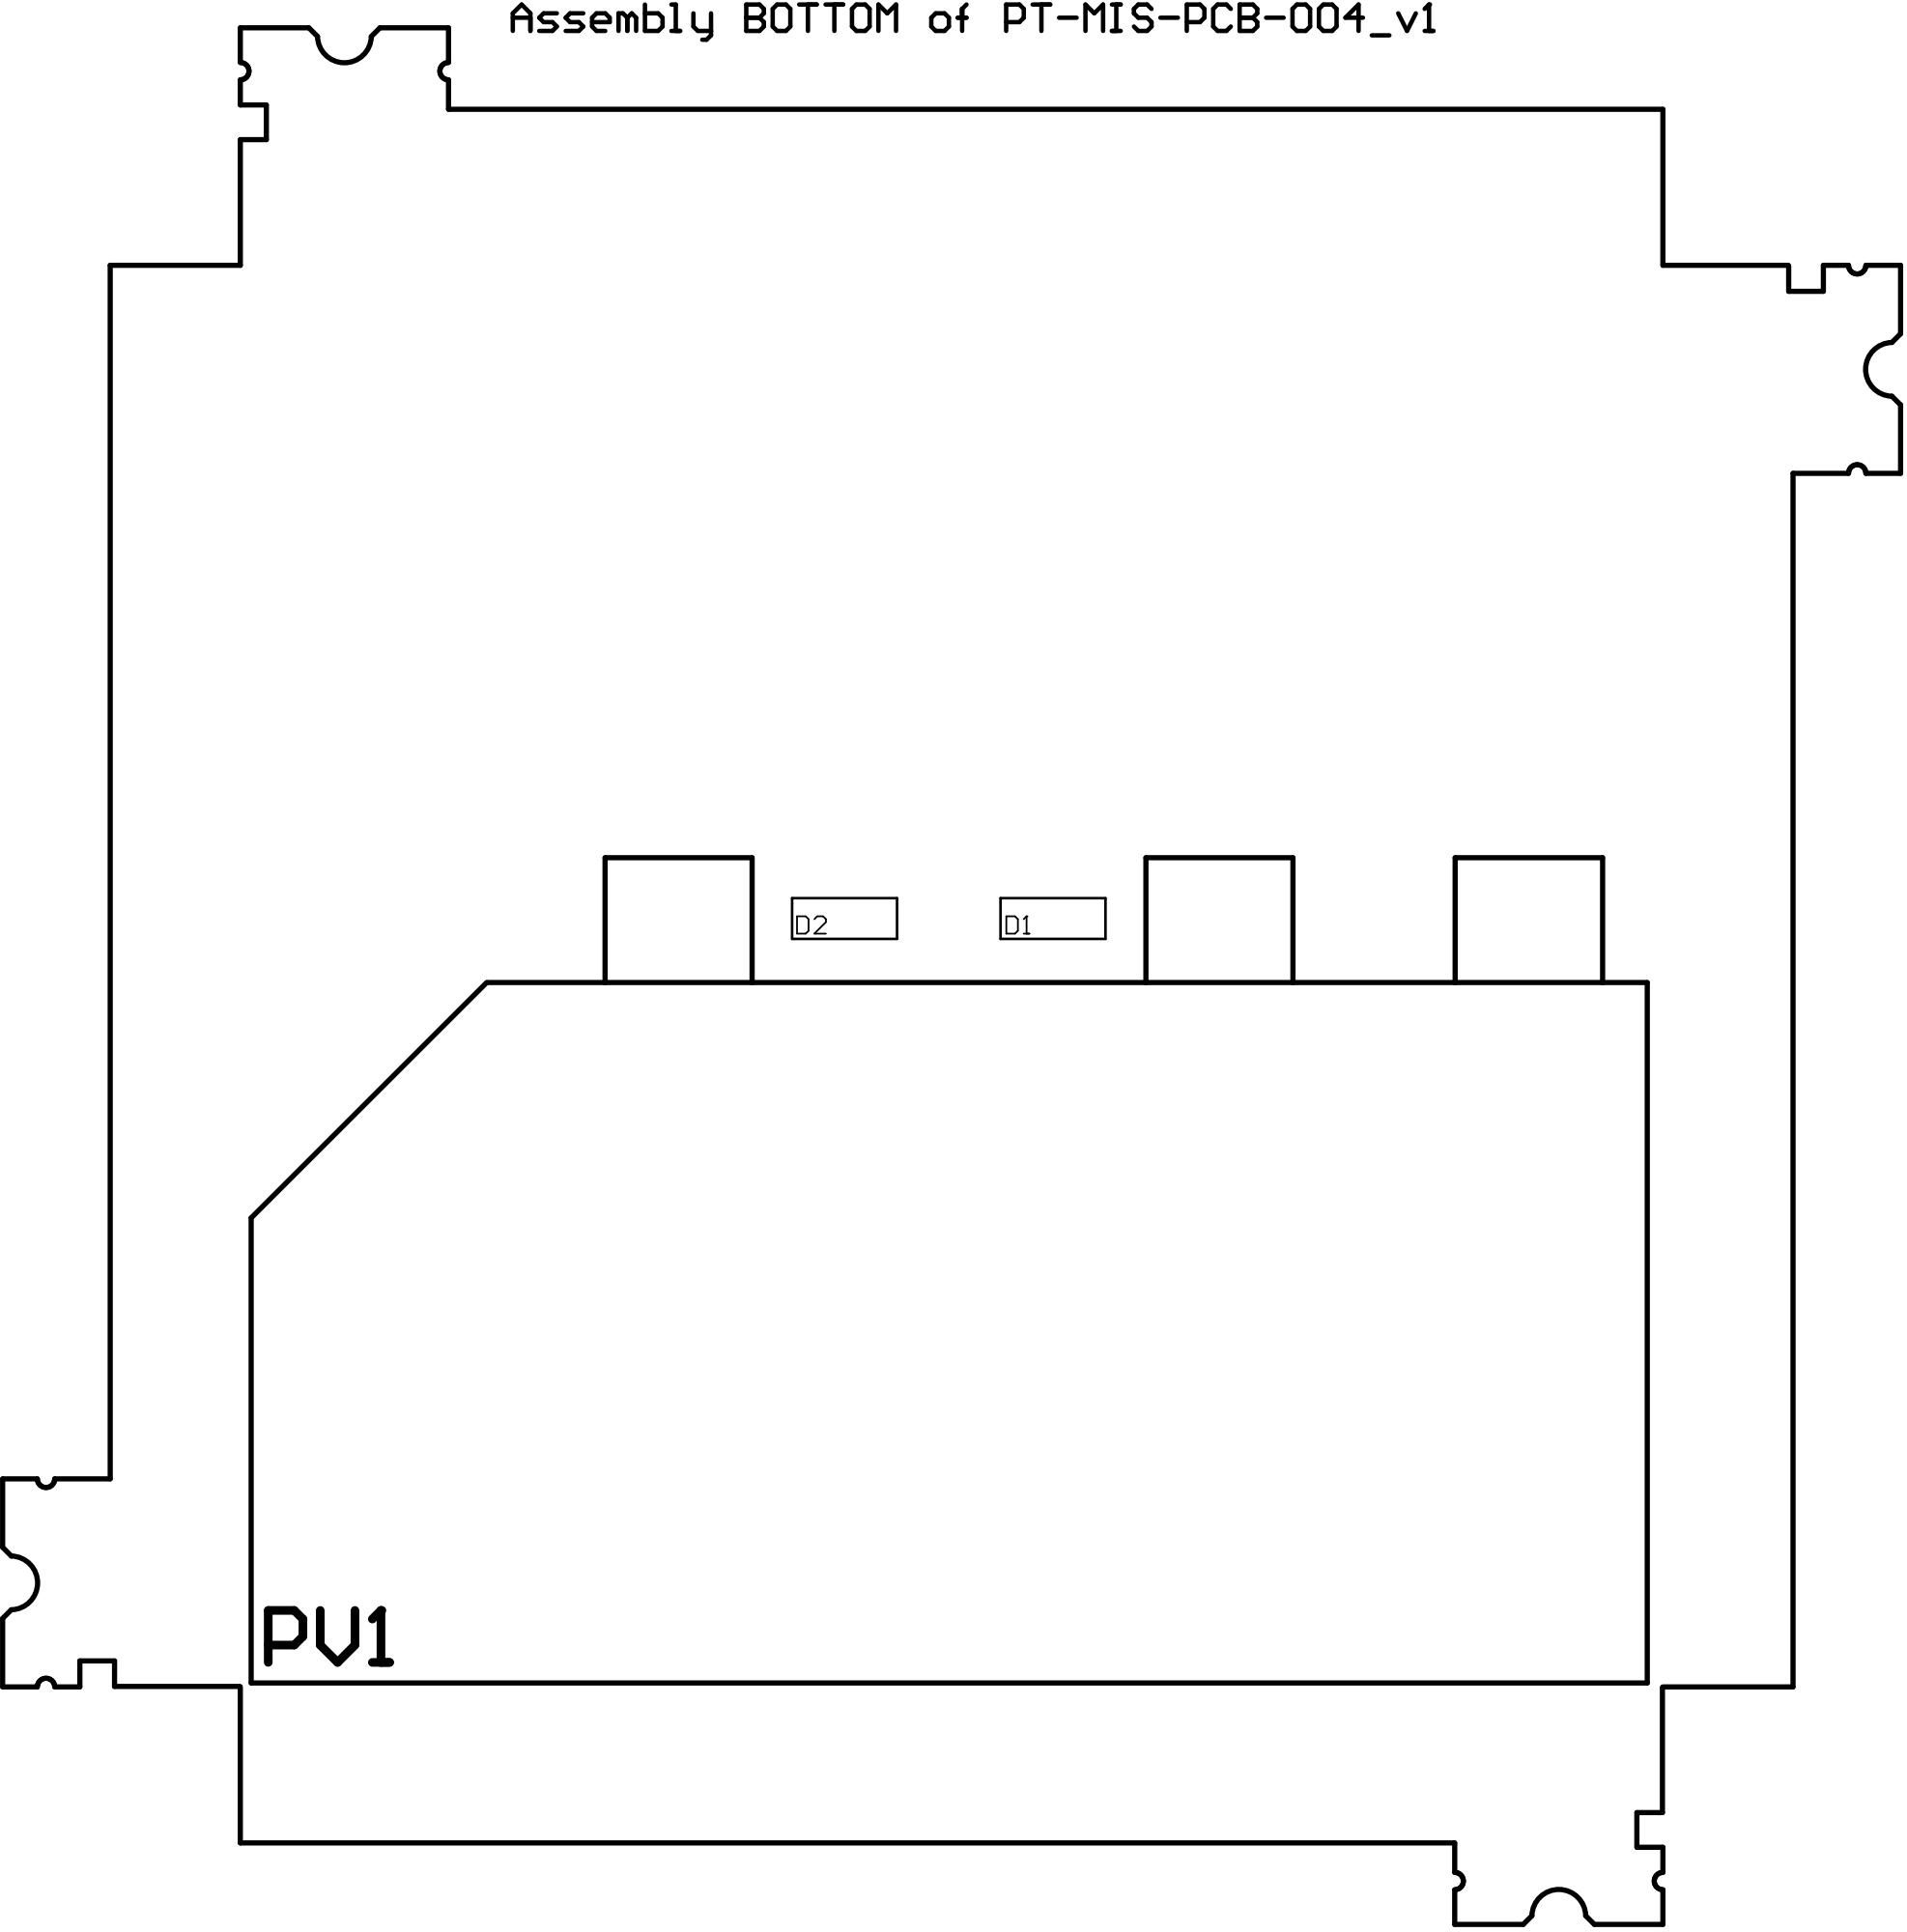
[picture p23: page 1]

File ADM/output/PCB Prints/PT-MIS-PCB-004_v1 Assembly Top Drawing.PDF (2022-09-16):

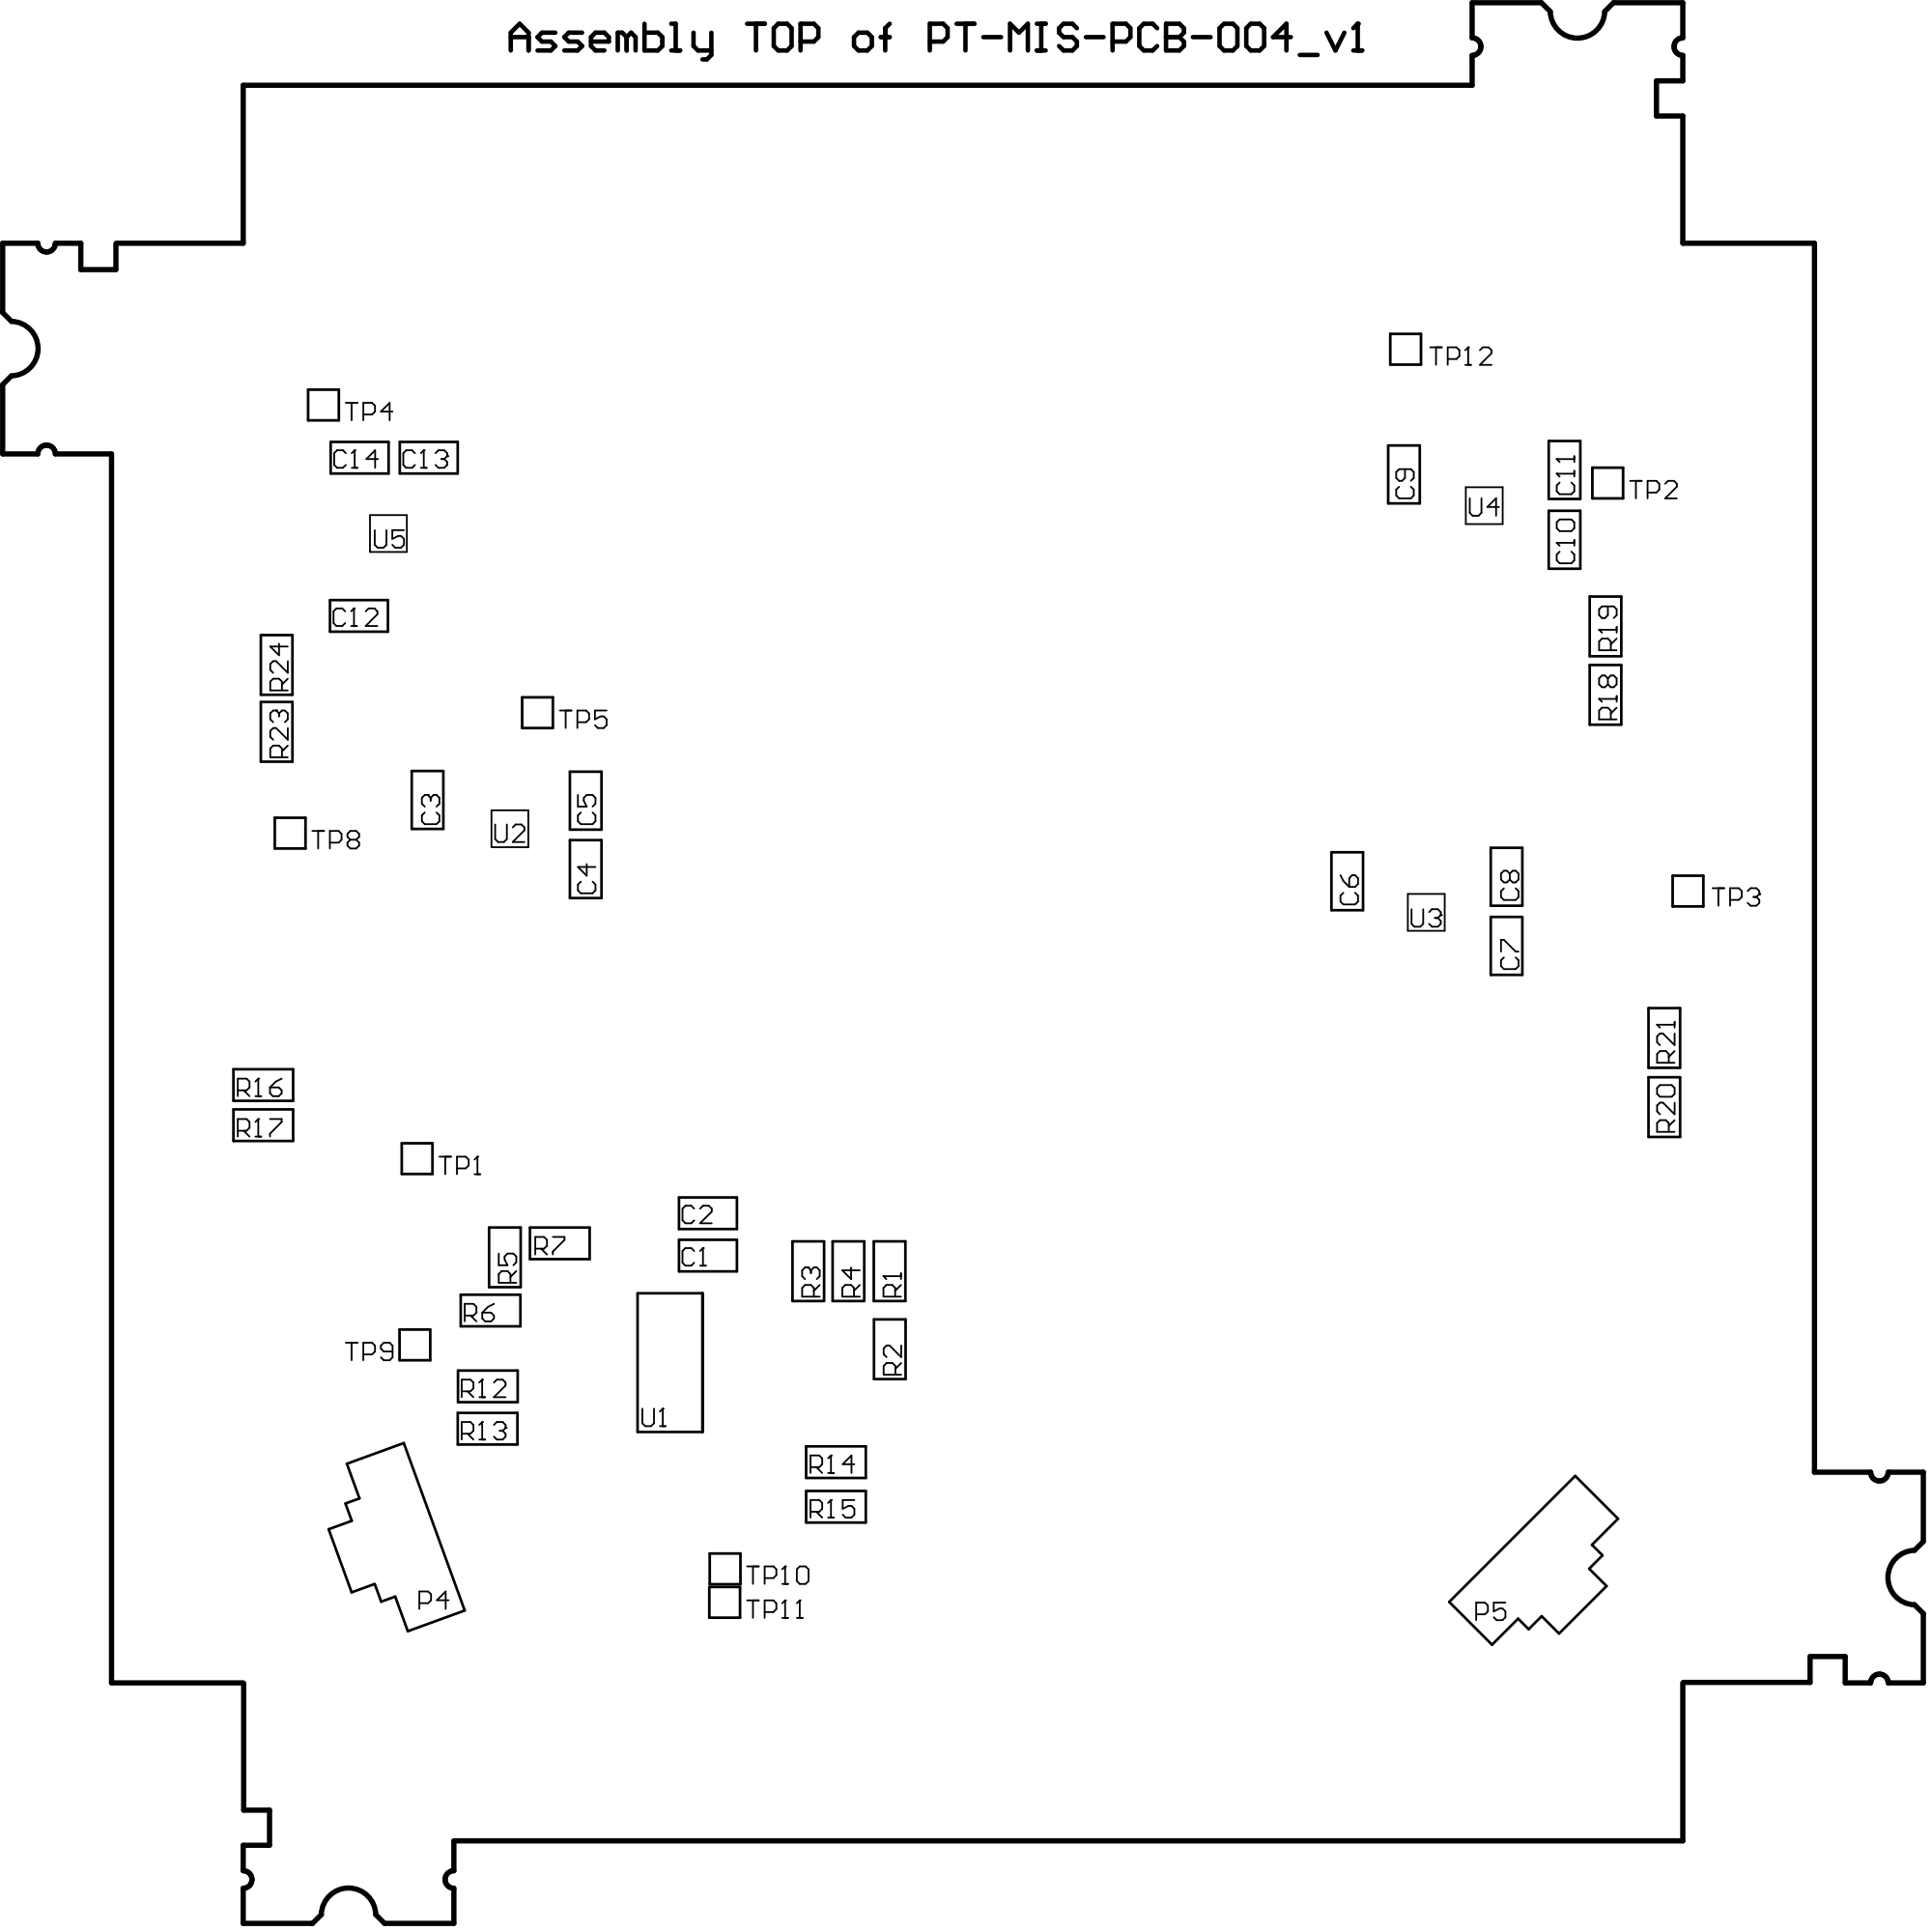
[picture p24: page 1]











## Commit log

2022-08-13 Added initial files for ADCS subsystem. Updated README files.
    [PT-MIS-PCB-001_v1 BOM Purchasing.xlsx, PT-MIS-PCB-001_v1 BOM Reference.xlsx, PT-MIS-PCB-001_v1 Project.SchDoc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]
2022-09-03 Added initial files for EPS subsystem.
    [PT-MIS-PCB-002_v1 BOM Reference-PT-PWR-EPS-002_v1.xlsx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]
2022-09-16 Added ADM design files. Modifications to READMEs.
    [PT-MIS-PCB-004_v1 BOM Purchasing.xlsx, PT-MIS-PCB-004_v1 BOM Reference.xlsx, PT-MIS-PCB-004_v1 Project.SchDoc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]
2022-09-20 Added NC Drill files to ADCS (#1)
2022-10-03 Added photo of PCB
2022-10-17 Addresses #7
    Moved I2C isolator into schematic with all other components, organizational changes only. Retroactively added revision history for 2019. Generated SCH PDF with these changes.
    [[03] - SCHEMATIC.SchDoc, [04] - REVISION HISTORY.SchDoc]
2022-10-17 Addresses #5
    Added block diagram from eps paper (Aguilar-Nadalini et al.), regenerated schematic PDF.
    [[02] - BLOCK DIAGRAM.SchDoc, [11] - REVISION HISTORY.SchDoc]
2022-11-01 Removed layer stackup (#2) from README and output for all subsystems.
    [PT-MIS-PCB-001_v1.xls]
